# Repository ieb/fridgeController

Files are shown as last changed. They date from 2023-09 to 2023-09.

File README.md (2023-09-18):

#  Fridge Controller

This is a controller for 12V Danfoss and Secomp fridges. The compressors on these fridges are
variable speed and typically have switch based external temperature sensors. In a low power
environment running off 12v there are a few problems, which can be addressed by buying one
of the top end control heads. Some of documentation for the newer compressors indicate that
the RPM and minimum battery voltages have more control, but the BD35 and BD50 compressors
while being variable speed have unsuitable battery shutoff voltages.

# Why ?

I've gone through 2x 300 Lead Acid battery sets due to the behavior of the Fridge Compressor, in the past 6 years. Perhaps 3 years is ok for flooded or AGM, but there have been perhaps 60 charge cycles per year, so 180 in total and the batteries have always been kept fully charged. Could be bad luck buying batteries claiming not to be what they are.... but they were not the cheapest and weighed almost the same as Rolls equivalents. (ie same volume of lead).

# Fridge hardware

The compressor (BD35) is a variable speed motor that runs at between 2000 and 3500 RPM. In basic setups
the speed is controlled current from one of the pins on the control unit of between 2mA (3500rpm) and 5mA (2000rpm).
Typically manufacturers add a fixed resistor to achieve this, loosing the benefits of variable speed control,
which allow these compressors to use significantly less energy than the fixed speed counterparts.

The controllers have a battery low voltage cutout which is set by another resistor. Typically this defaults to 10.7v but
can be lowered to 9.6v for solar only applications or 11.7v for other applications. All these voltages are sufficiently
low enough to damage most lead acid batteries, and certainly well below the manufacturer recommended minimum discharge
level of 12.2v. The saving grace is that many fridge cables will be long and there might be enough voltage drop to
disable the fridge before the damage is done (repeatedly). Second saving grace is after the damage is done the battery is
unlikely to maintain is voltage while the fridge is on and should drop to below these levels, switching the fridge off and
then recovering. Typically this is accompanied with low voltage alarms on other systems supplied by the same battery.

The control units for the compressor have a electronic CCU built in. It has a LIN interface (19200 baud 8-n-1 serial),
with the same electrical characteristics found on many K-LINE car interfaces in cars. Cheap pass-through K-LINE OBDII
adapters will almost certainly work. The protocol is similar to Modbus and allows access to almost all parameters, 
however the documentation on the format of the parameters is very sparse. There is a free windows utility xtool4cool, from
secop that allows access to the parameters, but, TBH, this interface is intended for manufacturing and is not worth the
effort to reverse engineer (imho).

The restive compressor control mentioned above can also be controlled by a 5KHz PWM signal driving an open collector NPN
transistor, the collector connected to the control pin. There are no specifications available on the duty cycle but I 
am going to assume the aim is to sink between 2mA and 5mA.

# This hardware

I thought about a Attiny3224, Atmega328p (Pro Mini) or ESP32, all are possible, but I dont want to have a screen as it 
draws too much power and needs buttons, and cant be hidden. Setup will be over serial. Attiny3224 and Atmega328p need a
serial adapter which is why the ESP32 is being chosen. If I want to run BLE then it will be enabled with a push button. 
Current draw on previous projects has been around 30mA which is ok given the Fridge when on draws 7A. When not connected
the onboard LED on the ESP32 indicates state... and if you want to know if the fridge is on... the compressor makes a sound. 

Control is maintained with 3 states, 0, 1, 2. Charging, Normal, Low Battery. On and off temperatures and compressor rpm
can be set for each state as cant a minimum charging and battery voltage. If the device enters a Low Battery state it can 
transition into the charging state when the minimum charging voltage is exceeded.

Voltages are measured with the ESP32 ADC via a voltage divider that keeps the ADC voltage < 2.5v and so in its linear range. (> 2.5 ESP32s ADC becomes quite non linear). The PWM output uses the wonderfully simple ESP32 led control API. For atMega and atTiny versions see the secoppower.cpp files for those chips. (That code has never been run so expect bugs in it).

The compressor RPM can be varied depending on the difference between measured temperature and target temperature. Temperature is measured over 1wire sensors which are so slow, but fast enough for this use. 1Wire measurements are using asynchronous requests.

# Compressor control.

Fridge circuits work by compressing the refrigerant, cooling it into a liquid form in a condensor, storing the refrigerant liquid in a reservoir. The liquid escapes through a metering device which lowers the pressure of the liquid. On entering the evaporator the liquid boils removing heat from the fridge. The gas returns to the compressor which re-compresses the gas back into a liquid.  Marine fridges tend to use a long capillary tube as the metering device, which is static. The reservwoir is generally quite small. Because the metering is fixed, there is little point in running the compressor at full speed exit temperature of the evaporator is low enough to generate frost, ie < 0C as that will only cool the atomsphere. So a temperature sensor at the exit of the evaporator could be used to control the speed of the compressor to ensure that only enough energy to is put into the compressor to cool the evaporator and not the pipes outside the fridge.  

## Temperature sensor locations.

* Input side of the evaporator, probably central - this is the default location on standard installation.
* Output side if the evaporator - outside the fridge but as far a away from the compressor as possible.
* Interior of fridge.

## Control mechanism.

Control of RPM should be based on the relative temperatures of the evaporator at both ends. The on and off temperature of the fridge should depend on the battery state, with the fridge being off if the voltage falls too low.

# Building

use pio command line and upload.

# Configuring

The serial port runs at 115200 8N1, press h for a menu with options. The PWM duty cycle to rpm mapping will need to be calabrated.

# PCB

Very simple schematic, see files in pcb/

# TODO

- [ ] build pcb
- [ ] hookup and test
- [ ] make use of the variable speed compressor
- [ ] Enable BLE
- [ ] Write Android or Chromium app.

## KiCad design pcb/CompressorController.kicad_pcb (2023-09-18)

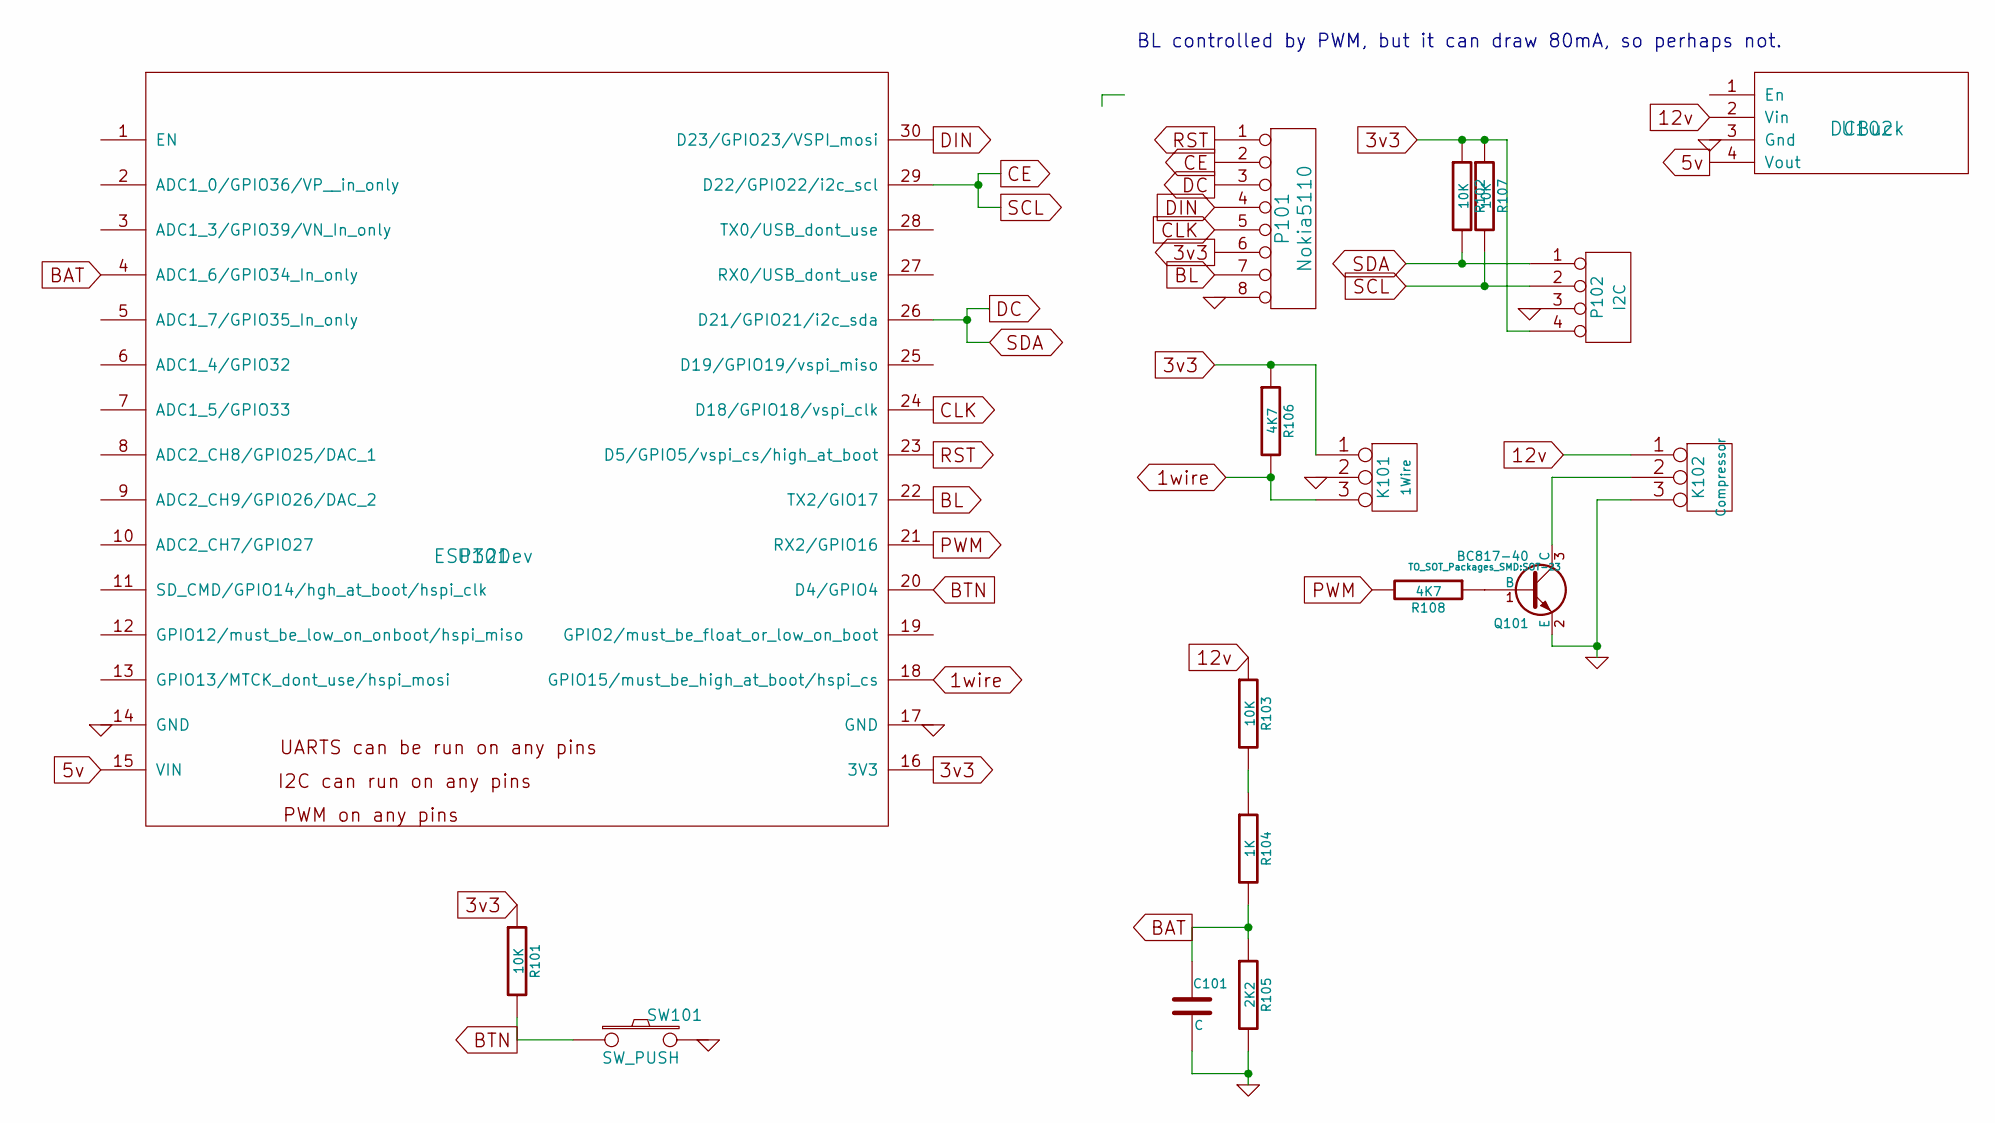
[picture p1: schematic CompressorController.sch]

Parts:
C101: C; C_0805_HandSoldering
K101: 1Wire; bornier3
K102: Compressor; bornier3
P101: Nokia5110; Pin_Header_Straight_1x08
P102: I2C; Pin_Header_Straight_1x04
Q101: BC817-40; SOT-23
R101, R102, R103, R107: 10K; R_0805_HandSoldering
R104: 1K; R_0805_HandSoldering
R105: 2K2; R_0805_HandSoldering
R106, R108: 4K7; R_0805_HandSoldering
SW101: SW_PUSH; SW_PUSH_6mm
U101: ESP32Dev
U102: DCBuck; DCBuckModule

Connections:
1wire: K101.3, R106.2, U101.18 (GPIO15/must_be_high_at_boot/hspi_cs)
3v3: K101.1, P101.6, P102.4, R101.1, R102.1, R106.1, R107.1, U101.16 (3V3)
5v: U101.15 (VIN), U102.4 (Vout)
12v: K102.1, R103.1, U102.2 (Vin)
BAT: C101.1, R104.2, R105.1, U101.4 (ADC1_6/GPIO34_In_only)
BL: P101.7, U101.22 (TX2/GIO17)
BTN: R101.2, SW101.1, U101.20 (D4/GPIO4)
CE: P101.2, P102.2, R107.2, U101.29 (D22/GPIO22/i2c_scl)
CLK: P101.5, U101.24 (D18/GPIO18/vspi_clk)
DC: P101.3, P102.1, R102.2, U101.26 (D21/GPIO21/i2c_sda)
DIN: P101.4, U101.30 (D23/GPIO23/VSPI_mosi)
GND: C101.2, K101.2 (PM), K102.3, P101.8, P102.3, Q101.2 (E), R105.2, SW101.2, U101.14 (GND), U101.17 (GND), U102.3 (Gnd)
unnamed: K102.2 (PM), Q101.3 (C)
unnamed: Q101.1 (B), R108.1
unnamed: R103.2, R104.1
PWM: R108.2, U101.21 (RX2/GPIO16)
RST: P101.1, U101.23 (D5/GPIO5/vspi_cs/high_at_boot)

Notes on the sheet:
BL controlled by PWM, but it can draw 80mA, so perhaps not.

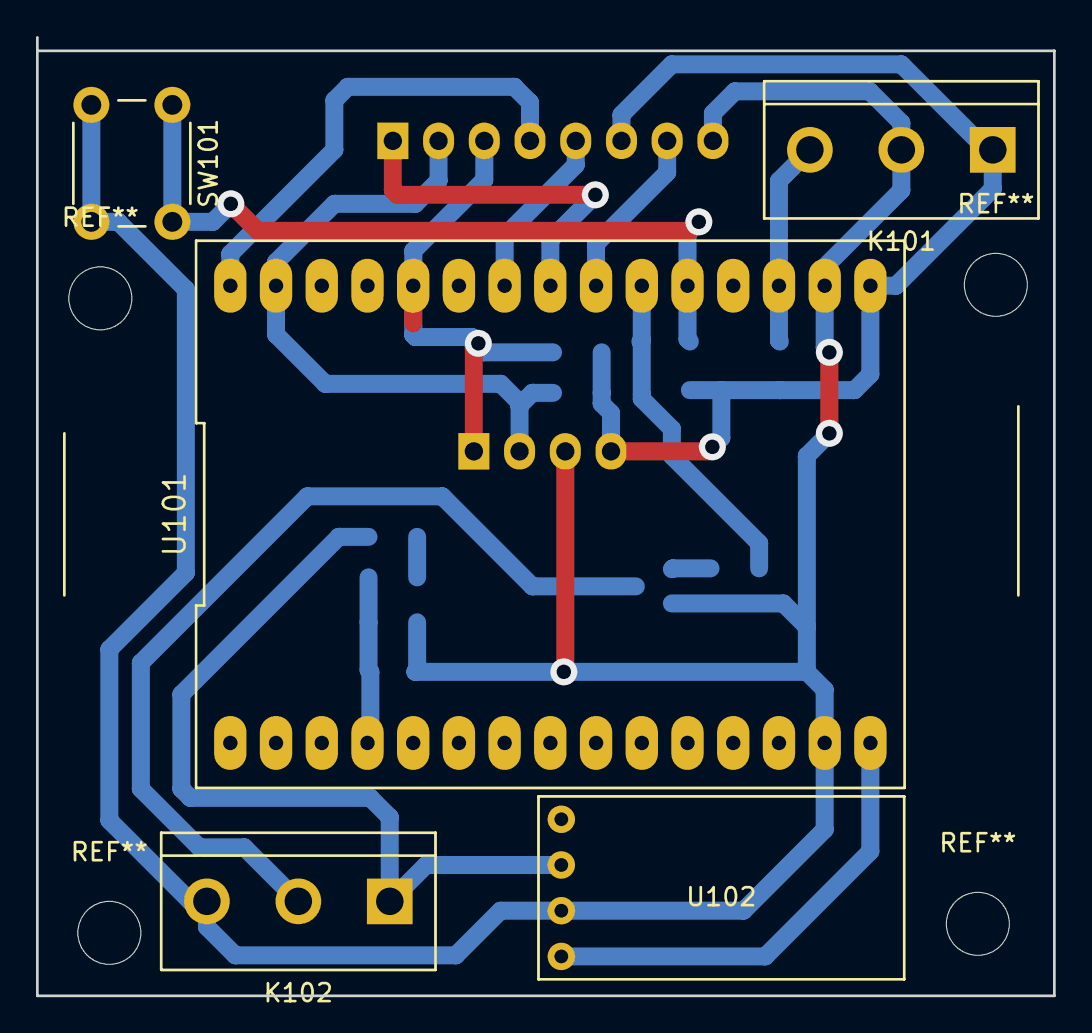
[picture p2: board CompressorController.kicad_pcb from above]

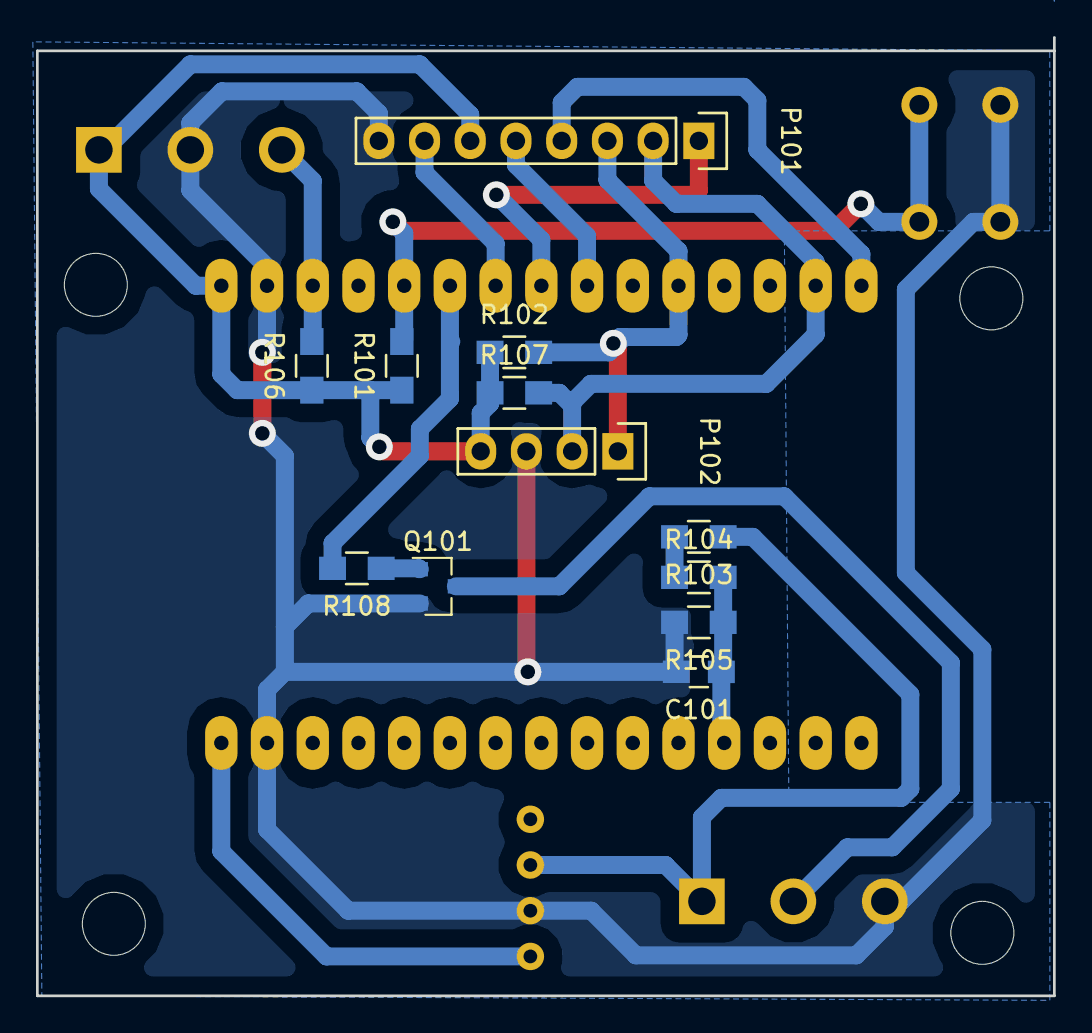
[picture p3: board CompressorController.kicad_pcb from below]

Board: 2 copper layers, 56.5 x 53.2 mm, 17 parts (12 on the bottom side), 17 nets.

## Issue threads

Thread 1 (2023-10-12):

Hey there! *This is not an issue 🤷🏻

doh38, 2023-10-12:
I have actually the same "fridge/freezer" clone and the same issues 😂🙏
I actually thought, why not completely bypass the controller? It's a bldc inside, it should theorically works.
So I plugged a vesc on the conpressor three phases, tweaked it a little bit and.. bam it does works 😍🔥
I want to integrate all sensor on an esp32 and simply control the vesc from it (I think) or maybe use all adc and directly control it from Lisp.
Your solution is way more elegant but.. I'm a vesc boy so.. 🥳✌️
Thanks for the docs awesome to see other people bringing the diy to these things 😎🙏
Have a nice day!

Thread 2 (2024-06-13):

There should be at least 10deg difference

motomarzel, 2024-06-13:
Hi,

From what I found, there should be between 10 and 20 deg difference between the temperature of the Evaporator and the setpoint (the one in the chamber). Which mean the evaporator should surely go under 0 deg.
That means the you should also include defrost cycle - time based or using temperature sensors to determine whether defrost is needed or not. I plan to install silicone heating pad behind the evaporator to do that - [like that one](https://www.aliexpress.com/item/1005006560247628.html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)

In order to preserve energy it may be good to consider cascaded PID control - one to control the compressor speed to reach desired Evaporator temperature and another to control the evaporator temperature (setpoint) according to chamber setpoint.
The other approach might be to use fuzzy logic+PID.

I am now working on the same project and plan to firstly do some datalogging to check which is the best approach.

I am also considering to install some temperature accumulating cool box Ice packs to reduce temperature fluctuation and (hopefully) safe some energy - https://www.funkyleisure.co.uk/kampa-cool-box-ice-pack---600ml-13333-p.asp

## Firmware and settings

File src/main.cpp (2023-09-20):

#include <Arduino.h>
#include "secoppower.h"
#include "tempsensor.h"
#include "battery.h"
#include "config.h"
#include "commandline.h"
#include "ssd1306.h"

ConfigSettings settings;
extern void showStatus(void);
extern void setRPM(int16_t rpm);
extern void setDutyCycle(int16_t dutyCycle);
CommandLine commandLine(&Serial, &settings, &showStatus, &setRPM, &setDutyCycle);
TemperatureSensors temperatureSensors;

SecopPower secopPower(&Serial, PWM_PIN, &(settings.config));

LCDDisplay lcdDisplay(&settings);



#define POWER_STATE_CHARGING 0
#define POWER_STATE_ON_BATTERY 1
#define POWER_STATE_LOW_BATTERY 2
const char * stateDisplay[3] = {
    "oncharge",
    "discharging",
    "low"
};


uint8_t state = POWER_STATE_ON_BATTERY;
bool compressorOn = false;
bool diagnosticsEnabled = true;
bool manualControl = false;
unsigned long compressorTurnedOnAt = 0;
unsigned long compressorTurnedOffAt = 0;

/**
 * Verifying to myself that the correct way to test for a time
 * difference in millis is (now - last ) > period
 * last is always before now, so that calculation will always
 * result in a positive difference when the unsigned long wraps
 * Other forms dont work
 *     now > (last + period) 
 * will fail when last approaches max long, since last + period wraps
 * now is always greater than the result.
 * Leaving here to remind myself.
 */
void testMillisDifference() {
    unsigned long t1 =  10;
    unsigned long t2 =  t1+9990;
    for (int i = 0; i < 100; i++) {
        t2++;
        Serial.printf("Low %lu %lu %lu  %s \n", t1, t2, (t2-t1), ((t2-t1)>10000UL)?"after":"before");
    }

    t1 =  4294967255;
    t2 =  t1+9990;
    for (int i = 0; i < 100; i++) {
        t2++;
        Serial.printf("High %lu %lu %lu %s \n", t1, t2, (t2-t1), ((t2-t1)>10000UL)?"after":"before");
    }

}

void setup() {
    Serial.begin(115200);
    // wait a second so that its possible to flash if the 
    // program is in a crashloop
    delay(1000);
    Serial.println("Secop Compressor Controller v1.0");
    temperatureSensors.begin();
    commandLine.begin();
    secopPower.begin();
    lcdDisplay.begin();
    Serial.println("press h for help");


}
void setDutyCycle(int16_t dutyCycle) {
    if ( dutyCycle == -1 ) {
        if ( manualControl ) {
            Serial.println("Switching to auto");
            manualControl = false;
            secopPower.setDutyCycle(0);
        }
    } else {
        if ( !manualControl ) {
            manualControl = true;
            Serial.println("Switching to manual duty cycle");
        }
        secopPower.setDutyCycle(dutyCycle);
        Serial.print("rpm set to ");Serial.println(secopPower.getCompressorRPM());
    }
}

void setRPM(int16_t rpm) {
    if ( rpm == -1 ) {
        if ( manualControl ) {
            Serial.println("Switching to auto");
            manualControl = false;
            secopPower.setCompressorSpeed(0);
        }
    } else {
        if ( !manualControl ) {
            manualControl = true;
            Serial.println("Switching to manual rpm");
        }
        secopPower.setCompressorSpeed(rpm);
        Serial.print("rpm set to ");Serial.println(secopPower.getCompressorRPM());
    }
}

void showStatus() {
    Serial.print("State                    : "); Serial.println(stateDisplay[state]);
    Serial.print("Control                  : "); Serial.println(manualControl?"manual":"auto");
    Serial.print("Voltage              (mV): "); Serial.println(readBatteryVoltageMv(BAT_ADC_PIN));
    Serial.print("Temperature Evaporator(C): "); Serial.println(temperatureSensors.readCelciusFromSensor(EVAPORATOR_SENSOR));
    Serial.print("Temperature Discharge (C): "); Serial.println(temperatureSensors.readCelciusFromSensor(DISCHARGE_SENSOR));
    Serial.print("Temperature Box       (C): "); Serial.println(temperatureSensors.readCelciusFromSensor(BOX_SENSOR));
    Serial.print("Compressor          (rpm): "); Serial.println(secopPower.getCompressorRPM());
    Serial.print("Temp High             (C): "); Serial.println(settings.config.turnOnTemperature[state]);
    Serial.print("Temp Low              (C): "); Serial.println(settings.config.turnOffTemperature[state]);
    Serial.print("Min Charging         (mV): "); Serial.println(settings.config.minimumChargingVoltage);
    Serial.print("Min Battery          (mV): "); Serial.println(settings.config.minimumBatteryVoltage);
}

/*
 * Aim is to return a  RPM based on the measured temperatures.
 * sensors are BOX_SENSOR, EVAPORATOR_SENSOR and DISCHARGE_SENSOR.
 * The fridge is a fridge not a freezer, so the simplest form of control
 * is to reduce the RPM of the fridge when the evaporator sensor says the 
 * evaporator is down to temperature.
 * 
 * ALso to stop cycling delay the turn on of the motor for 120s, and 
 * delay turning back on for 240s after a turn off.

    -D EVAPORATOR_SENSOR=0 
   -D DISCHARGE_SENSOR=1 
   -D BOX_SENSOR=2 

 * 
 */

int16_t calculateRPM(float *temperatures) {
    unsigned long now = millis();
    if ( compressorOn 
        && ((now - compressorTurnedOnAt) > settings.config.compressorStartDelay*1000)
        && ((now - compressorTurnedOffAt) > settings.config.compressorStartDelay*2000)  ) {
        if (temperatures[EVAPORATOR_SENSOR] <= settings.config.minEvaporatorTemperature
            || temperatures[DISCHARGE_SENSOR] <= settings.config.minDischargeTemperature ) {
            // not a freezer
            return 0;
        } else if (temperatures[EVAPORATOR_SENSOR] <= settings.config.targetEvaporatorTemperature ) {
            return 2000;
        } else {
            return map(temperatures[EVAPORATOR_SENSOR], settings.config.targetEvaporatorTemperature, 
                settings.config.highEvaporatorTemperature, 2000, 3500); 
        }
    }
    return 0;
}

void checkStatus() {
    static unsigned long last = millis();
    static unsigned long readSent = false;
    unsigned long now = millis();
    if ( !readSent && (now - last) > 7000UL ) {
        readSent = true;
        temperatureSensors.getTemperatures();
    } 
    if ( readSent ) {
        temperatureSensors.checkStatus();
    }
    if ( (now - last) > 10000UL ) {
        if ( !temperatureSensors.checkStatus() ) {
            Serial.println("Onewire too slow");
        }
        last = now;
        readSent = false;
        float  voltage = readBatteryVoltageMv(BAT_ADC_PIN);
        // determine any state change.
        switch(state) {
            case POWER_STATE_CHARGING:
                // can go into on battery.
                if ( voltage < settings.config.minimumChargingVoltage ) {
                    state = POWER_STATE_ON_BATTERY;
                    Serial.print("Below minimum charging voltage  bv:");
                    Serial.print(voltage);
                    Serial.print(" <  min:");
                    Serial.println(settings.config.minimumChargingVoltage);
                }
            break;
            case POWER_STATE_ON_BATTERY:
                // can go into low power or charging.
                if ( voltage > settings.config.minimumChargingVoltage ) {
                    state = POWER_STATE_CHARGING;
                    Serial.print("Above minimum charging voltage  bv:");
                    Serial.print(voltage);
                    Serial.print(" >  min:");
                    Serial.println(settings.config.minimumChargingVoltage);
                } else if ( voltage < settings.config.minimumBatteryVoltage ) {
                    state = POWER_STATE_LOW_BATTERY;
                    Serial.print("Below minimum battery voltage  bv:");
                    Serial.print(voltage);
                    Serial.print(" <  min:");
                    Serial.println(settings.config.minimumBatteryVoltage);
                }
            break;
            case POWER_STATE_LOW_BATTERY:
                // in low battery mode, only way out is to to be charged.
                // the battery voltage will recover, but the fridge should 
                // reduce its drain once this happens.
                if ( voltage > settings.config.minimumChargingVoltage ) {
                    state = POWER_STATE_CHARGING;
                    Serial.print("Above minimum charging voltage  bv:");
                    Serial.print(voltage);
                    Serial.print(" >  min:");
                    Serial.println(settings.config.minimumChargingVoltage);
                }
            break;
        }
        float temperatures[3];
        for (int i = 0; i < 3; i++) {
            temperatures[i] = temperatureSensors.readCelciusFromSensor(i);

        }
        int16_t rpm = 0;
        if ( state == POWER_STATE_LOW_BATTERY ) {
                secopPower.setCompressorSpeed(0);
                compressorOn = false;
        } else {
            if ( temperatures[BOX_SENSOR] > settings.config.turnOnTemperature[state] ) {
                if ( !compressorOn ) {
                    compressorTurnedOnAt = millis();
                    compressorOn = true;
                }
                rpm = calculateRPM(temperatures);
                secopPower.setCompressorSpeed(rpm);
            } else if ( temperatures[BOX_SENSOR] < settings.config.turnOffTemperature[state]) {
                if ( compressorOn ) {
                    compressorTurnedOffAt = millis();
                    compressorOn = false;
                }
                secopPower.setCompressorSpeed(0);
            }        
        }
        lcdDisplay.update(voltage,  temperatures, rpm, state);

    }
}

void flashLed() {
    static unsigned long last = millis();
    static unsigned long cycle = 0;
    unsigned long now = millis();
    if ( (now-last) > last ) {
        last = now;
        int8_t ledOn = (cycle%2);
        switch(state) {
            case POWER_STATE_CHARGING:
                // 3 flashes
                if ( cycle > 5 ) {
                    ledOn = 0;
                }
                break;
            case POWER_STATE_ON_BATTERY:
                // 2 flashes
                if ( cycle > 3 ) {
                    ledOn = 0;
                }
                break;
            case POWER_STATE_LOW_BATTERY:
                // flash 1x
                if (cycle > 1 ) {
                    ledOn = 0;
                }
                break;

        }
        digitalWrite(LED_PIN, (ledOn==1)?HIGH:LOW);
        cycle++;
        if ( cycle > 10 ) {
            cycle = 0;
        }
    }

}

void loop() {
    checkStatus();
    flashLed();
    lcdDisplay.update();
    diagnosticsEnabled = commandLine.checkCommand();
    temperatureSensors.diagnosticsEnabled = diagnosticsEnabled;
    settings.diagnosticsEnabled = diagnosticsEnabled;
}

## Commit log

2023-09-18 Added display
    [CompressorController.kicad_pcb, CompressorController.sch]
2023-09-20 Switched to using nvs for config
